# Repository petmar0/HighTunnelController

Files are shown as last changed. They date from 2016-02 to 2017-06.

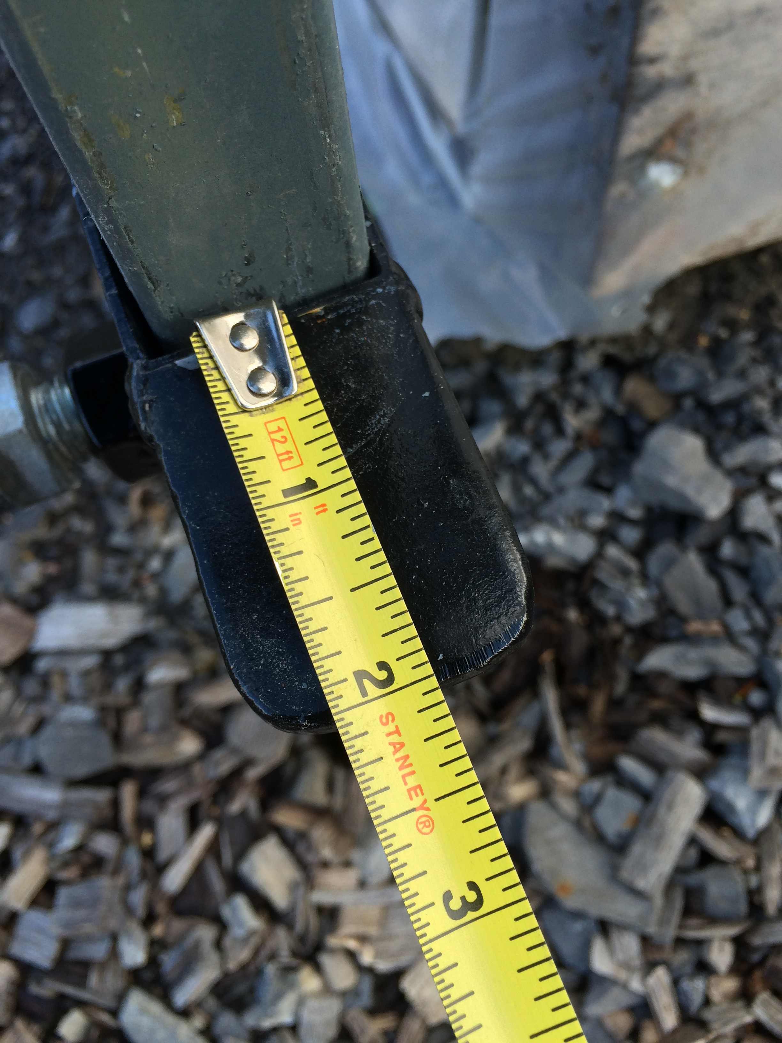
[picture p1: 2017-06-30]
TheManInTheHighTunnel/Winch Measurements 2.JPG

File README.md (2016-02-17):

# HighTunnelController

Control Flow
The setup method configures SD card and reads config file values from live.cfg
If you want to change config values you can edit live.cfg on the SD card manually or use the program to edit it

After starting up the program outputs instructions to the serial monitor and waits for your input 
* You can (and should) set the date/time
* You can read sensor values to test the sensors out
* You can control the motors to test them out
* You can read and erase the config file and the log file
* You can write new values to the config file
* You can start the main high tunnel control program running

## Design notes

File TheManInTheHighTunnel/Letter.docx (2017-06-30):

Pete Marchetto

160B Riley Robb Hall

111 Wing Dr.

Ithaca, NY 14853

201.403.5470

pmm223@cornell.edu

October 29, 2015

Dr. Joshua Cerra

444 Kennedy Hall

Ithaca, NY 14853

Dear Dr. Cerra,

This letter is to confirm the specification that we discussed yesterday. You are asking for a system that is capable of controlling the temperature within a high tunnel to stay a set amount above the external ambient temperature.

The system:

- shall be capable of regulating the internal temperature of a high tunnel to stay at 5.0±0.5 °F above the external ambient temperature.
- shall be capable of operating in temperatures between -20 to 130 °F.
- shall make use of two winches (T2000, SuperWinch, Putnam, CT), each of which consumes a maximum of 0.5 kW, to trim the wall height of the high tunnel for ventilation and heating or cooling.
- shall further use two ventilation fans (yet to be specified) to draw in air at a rate no less than 500 CFM to cool the high tunnel.
- shall be capable of running on solar power only in an environment with a maximum insolation power of 2 kWh/m²/Day (NREL, 2005).
- shall be fully compliant with the IP66W rating, and shall have its sensitive electronics enclosed in a NEMA 4 or 4X series enclosure.
- shall have a thermal mass element to keep temperatures sufficiently high at night comprised of a minimum of 3 gal./sqft. for the south wall of the high tunnel, comprising a total of 15 55 gallon drums or 20 35 gallon drums.

Please review this specification and get back to me with any comments or corrections so that we might proceed expeditiously to component selection.

Sincerely,

Pete Marchetto

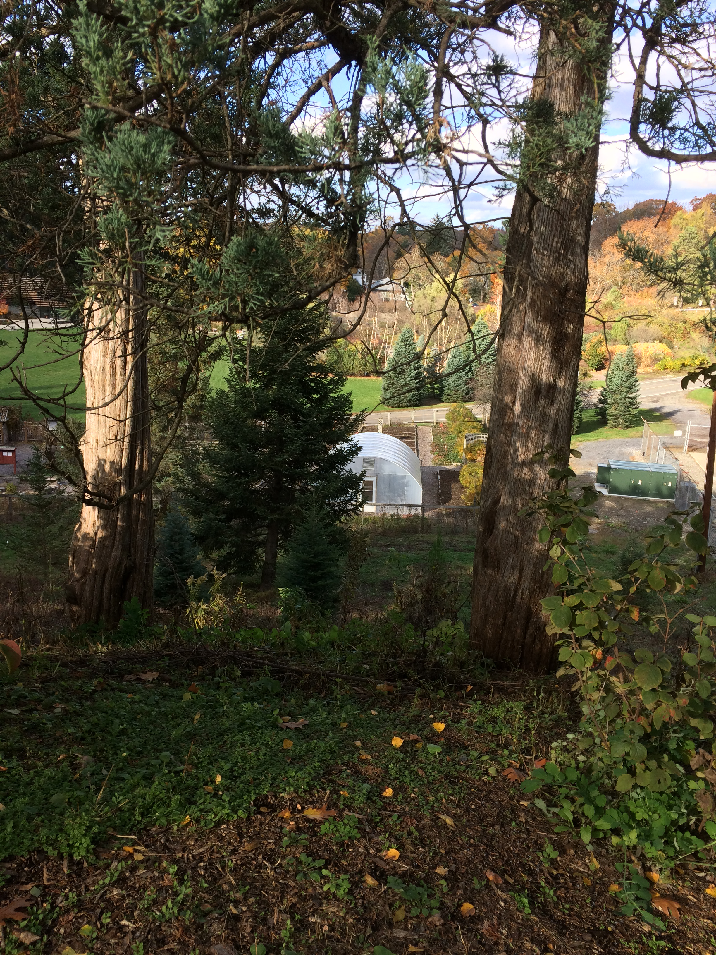
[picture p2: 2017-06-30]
TheManInTheHighTunnel/Sunlight from Above 2.JPG

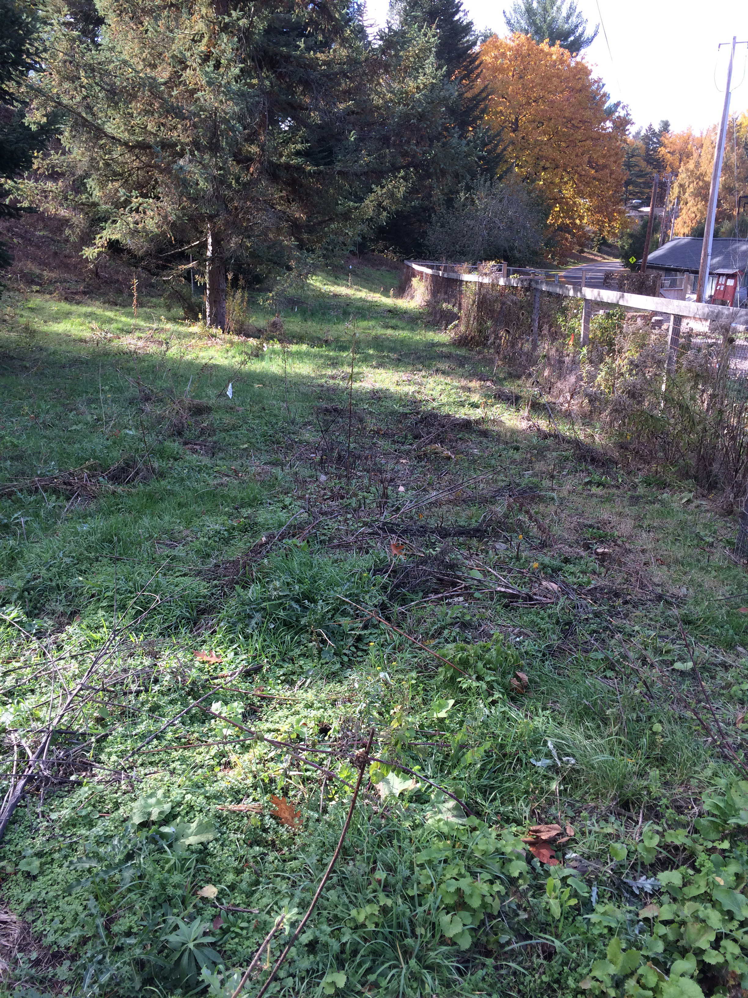
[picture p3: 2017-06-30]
TheManInTheHighTunnel/Sunlight on Fence 5.JPG

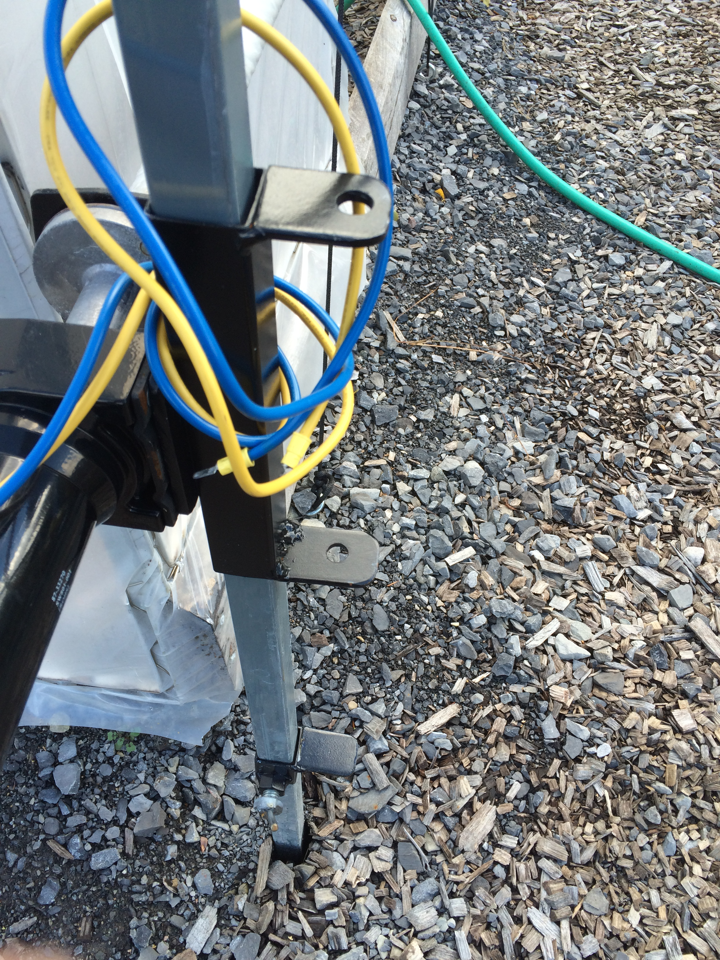
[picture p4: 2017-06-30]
TheManInTheHighTunnel/Winch Detail 1.JPG

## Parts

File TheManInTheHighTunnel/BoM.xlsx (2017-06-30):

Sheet: Summary
Sensing | $800.00
Enclosure | $300.00
Power | $1865.00
Control | $320.00
Fans | $940.00
Thermal | $130.00
Total | $4355.00

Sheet: Enclosure
Item | Make | Model | Quantity | Price |  | Extended Price | URL | Dimensions | Purpose
Waterproof Box | Pelican | iM2100 | 2 | $100.00 | not ordered | $200.00 | http://www.pelican.com/us/en/product/watertight-storm-hard-cases/small-case/standard/iM2100/ | At least 10x14x6 | Keep circuits safe and dry | Did not order - need to find dealer in this area
High Current (45A 12V min) 2 wire connectors | Conxall/Switchcraft | 4182-2PG-300 | 10 | $10.00 | not ordered | $100.00 | http://www.digikey.com/product-search/en?keywords=4182-2PG-300 |  | Connectors for motors and actuators | Not clear what needs to be ordered
Low Current (1A) 2 wire connectors | Amico | M14-4 | 10 | $15.00 | not ordered | $150.00 | http://www.amazon.com/M14-4-Waterproof-Connector-Connect-Adpater/dp/B00HR6M98Q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 |  | Connectors for limit switches and PV monitor | Not clear what needs to be ordered
Low Current (1A) 3 wire connectors | Amico | M14-4 | 10 | $15.00 | not ordered | $150.00 | http://www.amazon.com/M14-4-Waterproof-Connector-Connect-Adpater/dp/B00HR6M98Q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 |  | Connectors for temperature sensors
Super High Current (85 A 12V min) 2 wire connector | Conxall/Switchcraft | 4182-2PG-300 | 2 | $10.00 | not ordered | $20.00 | http://www.digikey.com/product-search/en?keywords=4182-2PG-300 |  | Connector for battery
Total |  |  |  |  |  | $300.00

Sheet: Power
Item | Make | Model | Quantity | Price |  | Extended Price | URL | Notes
backup battery | ExpertPower | EXPT1250 | 1 | $20.00 | ordered | $20.00 | http://www.amazon.com/ExpertPower-EXP1270-Black-Rechargeable-Battery/dp/B003S1RQ2S | sealed lead acid battery (12V, 6Amh)
Marine Deep Cycle Battery | VMAXTANKS | MR-86-50 | 2 | $150.00 | ordered | $300.00 | http://www.amazon.com/VMAXTANKS-MR86-50-Performance-Navigator-Trolling/dp/B009UE6NY4 | 50 Amh, 12 V
thin wire |  |  | 1 | $30.00 | not ordered | $30.00 | http://www.grainger.com/product/GRAINGER-APPROVED-Music-Wire-5XE99?s_pp=false | 16 gage or lower, 2 conductor, 250 feet
heavy duty wire |  |  | 1 | $300.00 | not ordered | $300.00 | http://www.grainger.com/product/AFC-MC-CABLES-12-AWG-Armored-Cables-WP5969589/_/N-/Ntt-armored+cables+12-2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 | armored cable, 16 gage or lower, 2 conductor, 250 feet
heavy duty hi amp wire |  |  | 1 | $150.00 | not ordered | $150.00 | http://www.grainger.com/category/building-wire/wire-and-cable/wire-cable-and-carrier-systems/electrical/ecatalog/N-qs4Z1z0mlns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 | 6WG or lower, exterior, 1 conductor, 150 feet
charge controller | Renogy |  | 1 | $45.00 | ordered | $45.00 | http://www.amazon.com/Renogy-Amp-Solar-Charge-Controller/dp/B00BCTLIHC | 20 amh
Panels | Renogy |  | 6 | $150.00 | only ordered 2 | $900.00 | http://www.amazon.com/Renogy-Watts-Volts-Monocrystalline-Solar/dp/B009Z6CW7O | 100 W
Cable Connectors (45 A) | Connxall | 3182-2SG-3DC | 10 | $10.00 | not ordered | $100.00 | http://www.mouser.com/Search/Refine.aspx?Keyword=3182-2SG-3DC
Cable Connectors (85 A) | Connxall | 3282-4SG-3DC | 2 | $10.00 | not ordered | $20.00 | http://www.mouser.com/ProductDetail/Conxall-Switchcraft/6282-4SG-3DC/?qs=I3kMT7EEIOUfaAjga64oJA%3D%3D
Total |  |  |  |  |  | $1865.00

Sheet: Sensing
Item | Make | Model | Quantity | Price |  | Extended Price | URL
Temp Sensor | Texas Instruments | LM35CAZ/NOPB-ND | 10 | $10.00 | not ordered | $100.00 | http://www.digikey.com/product-detail/en/LM35CAZ%2FNOPB/LM35CAZ%2FNOPB-ND/148180
Limit Switch | Panasonic | AZH2332 | 10 | $40.00 | not ordered | $400.00 | http://www.digikey.com/product-search/en?keywords=azh2332
Cable Connector Cord | Panasonic | AZH28113 | 10 | $30.00 | not ordered | $300.00 | http://www.digikey.com/product-search/en?keywords=AZH28113
Total |  |  |  |  |  | $800.00

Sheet: Control
Item | Make | Model | Quantity | Price |  | Extended Price | URL | Dimensions
Relay | Sainsmart | B0057OC66U | 10 | $20.00 | ordered 5 | $200.00 | http://www.amazon.com/gp/product/B0057OC66U/ | 8x6x2
Board | Wildfire | v3 | 2 | $50.00 | ordered | $100.00 | http://shop.wickeddevice.com/product/wildfire/ | 4x3x2
PIR Sensors | MPJA | HC-SR501 | 10 | $2.00 | ordered 4 | $20.00 | http://www.amazon.com/2013newestseller-HC-SR501-Pyroelectric-Infrared-Detector/dp/B00FDPO9B8?rps=1
Total |  |  |  |  |  | $320.00

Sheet: Fans
Item | Make | Model | Quantity | Price |  | Extended Price | URL
Actuators | CfD | CFD-DLA2 | 2 | $10.00 | ordered | $20.00 | http://www.amazon.com/gp/product/B00CZBQCR2
Fans | Backwoods Solar | F20-PLUS | 2 | $460.00 | ordered | $920.00 | http://www.backwoodssolar.com/products/fans-large-small/large-dc-super-fan-20inch-12-24v
Total |  |  |  |  |  | $940.00

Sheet: Thermal
Item | Make | Model | Quantity | Price |  | Extended Price | URL
Lime | Espoma | GL6 | 2 | $5 | ordered | $10 | http://www.amazon.com/Espoma-GL6-Garden-Amendment-6-75-Pound/dp/B0063ZDTI6
Barrels |  | 35 Gal. | 2 | $40 |  | $80
Hose | Gilmour | Flexogen 100 | 1 | $40 | ordered | $40 | http://www.amazon.com/Gilmour-Flexogen-Hose-Inch-10012100/dp/B000NCWOKE
Total |  |  |  |  |  | $130

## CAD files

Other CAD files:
TheManInTheHighTunnel/Thermal Mass System.skp

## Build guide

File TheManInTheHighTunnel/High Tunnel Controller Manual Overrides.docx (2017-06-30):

High Tunnel Controller Manual Overrides

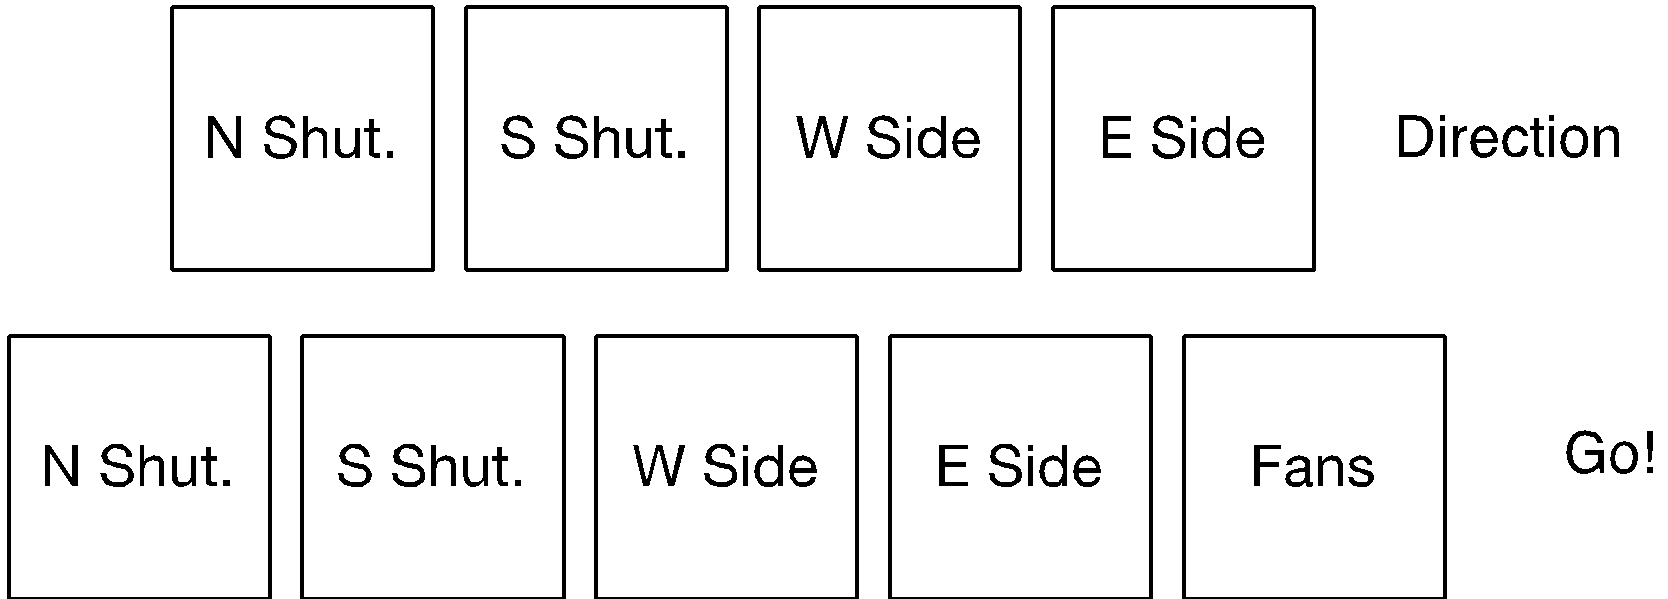
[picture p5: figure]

Default direction states: shutters, opening; sides, closing.

To open shutters, press their go relays (bottom row). To close shutters, hold down their direction relays (top row) while pressing their go relays. The return springs should hold the shutters in their last set position.

To close sides, press their go relays (bottom row). To open sides, hold down their direction relays (top row) while pressing their go relays.

The fans can only be turned on momentarily by manually overriding their go relay, but this is useful for testing them.

WARNING: There are no limit controls or safety devices to stop the sides when they are engaged manually. Make certain that all people in the vicinity are clear, and that you stop the sides before they reach their upward or downward limit of travel.

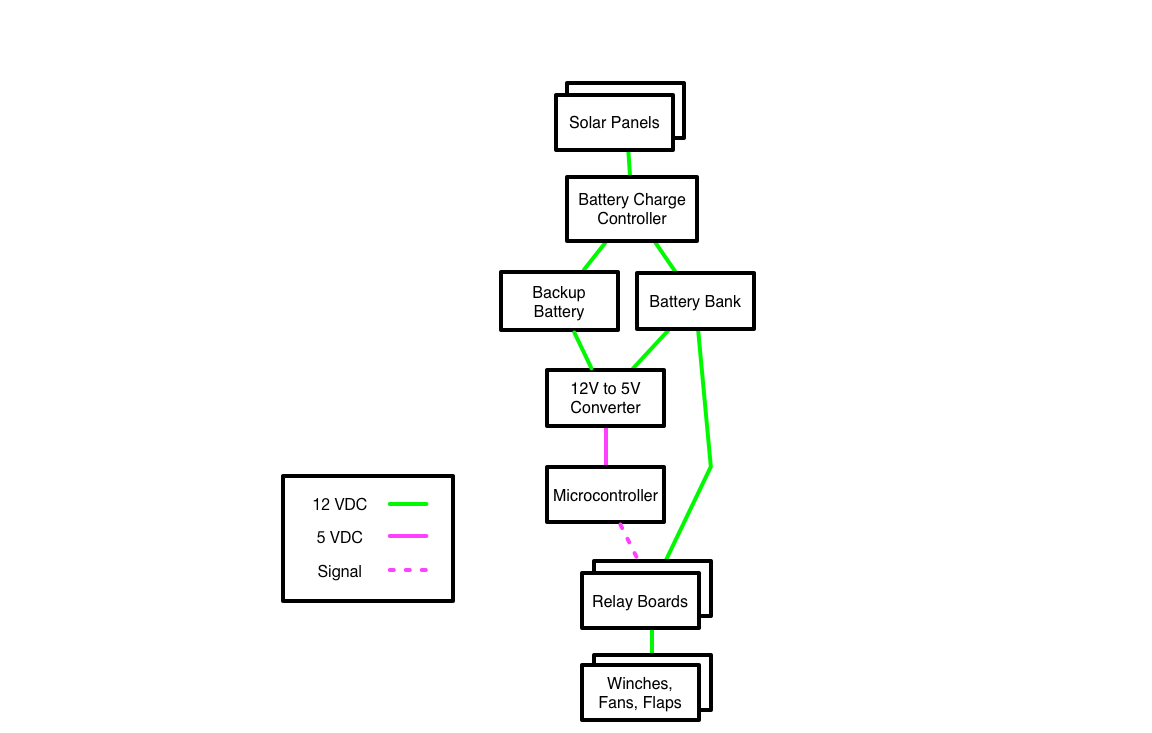
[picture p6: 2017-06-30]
TheManInTheHighTunnel/Power/power wiring diagram.png

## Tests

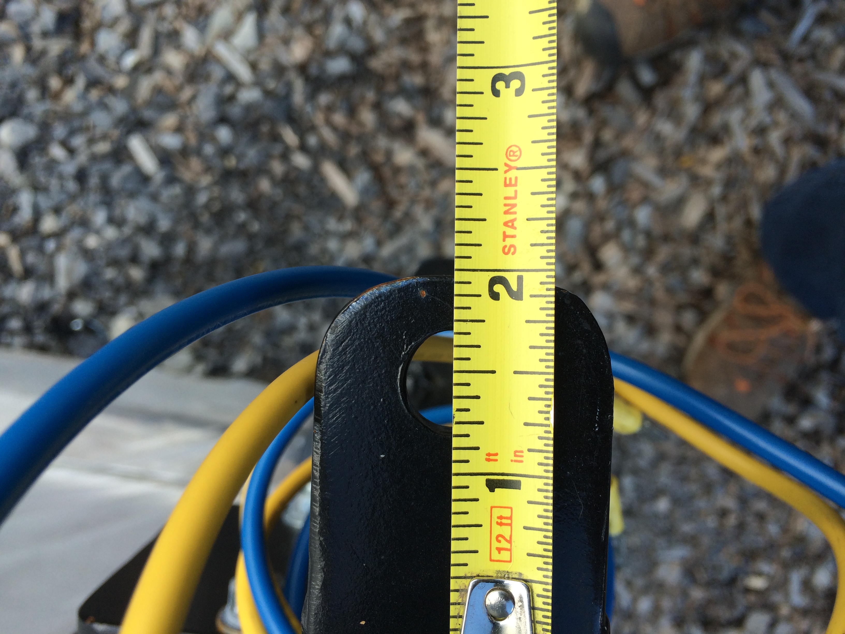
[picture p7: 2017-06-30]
TheManInTheHighTunnel/Winch Measurements 3.JPG

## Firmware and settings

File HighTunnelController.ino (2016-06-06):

#include <Time.h>
#include <SD.h>
#include <WildFire.h>
#include <Wire.h>
// #include "RTClib.h"

// Constants used by program, note that the file names are essentially constants but specifying that causes an error
const unsigned long MIN_ALLOWABLE_DATE_TIME = 1420156799; // 1 second before Jan 1 2015 GMT
const unsigned long MAX_ALLOWABLE_DATE_TIME = 1893520800; // Jan 1 2030 GMT
const unsigned long SECONDS_IN_HOUR         = 3600;
char configFileName[] = "live.cfg"; // recommended to leave this set and rename a different file as live.cfg to update it
char logFileName[] = "live.log"; // recommended to leave this set.  Multiple log files will be spun off as we go.
char heatWaveFileName[] = "heat.log"; // recommended to leave this set. This is where heatwave data is logged explicitly.

// External variables that can be passed in via config file
int gmt_hour_offset = -5; // -5 is the EST offset
float too_hot_delta = 6.0;  // If difference between inside and outside temp is more than this start to cool
float way_too_hot_delta = 7.5; // If difference between inside and outside temp is more than this use more aggressive cooling measures
float too_cool_delta = 4.0; // If difference between inside and outside temp is less than this start to warm
float super_cool_delta = -1.0; // If difference between inside and outside temp is less than this and warm up inside using outside air
boolean disable_log_file = false; // setting this to true disables writing to log file. Can help debug memory card issues
boolean manual_sensor_entry_mode = false; // If true then read sensors from Serial input by user instead of actual sensors.  Used to test system.
char temperature_units = 'F'; // Set ot F for Farenheight of C for Celcius.  If you change this you should probably change the deltas too.
int heat_wave_temperature = 90; // Temperature at which tunnel is considered a heatwave. WARNING if you update temperature units to C you MUST update this as well
int heat_wave_enabled_warming_temperature = 95; // When heat wave is enabled keep warming tunnel till it hits this. Should be enough above heat_wave_temperature to ensure it doesm't cool down below it
int heat_wave_enabled_cooling_temperature = 99; // When heat wave is enabled cool if tunnel gets above this. If outside is hot the keep up with that temp instead
int heat_wave_hours_to_log = 6; // How many consecutive hours temp must be above heat_wave_temperature to count as a heat wave day
int heat_wave_days_to_log = 3; // How many consecutive heat wave days must happen to count as a heat wave
int heat_wave_switch_pin = 12; // Pin the switch to enable heat wave mode is connected to
int pir_sensor_pin = A6; // Pin that PIR motion sensors that ensure no one is around while sides roll are connected to.
int pir_wait_time_max_seconds = 10; //If PIR sensors detect someone this is how long we'll wait before we give up and accept that we cannot roll
int pir_milliseconds_between_checks = 1000; //How long to wait between sampling the PIR sensors again when someone is detected, also how long to do a continuous sample for movement
int inside_temp_sensor_pin = A2; // Analog pin that temperature sensor inside the high tunnel is connected to
int outside_temp_sensor_pin = A1; // Analog pin that temperature sensor outside the high tunnel is connected to
unsigned long millisecond_delay_between_actions = 5000; // How long to wait between reading temperature and taking action to correct it
int winch_roll_seconds = 7; // How many seconds to roll each winch at a time
int winch_roll_milliseconds_between_limit_check = 100; // How long to wait between checking limit sensors while rolling
int fan_run_seconds = 20; // How how long to run fans at a stretch
int east_winch_roll_direction_digital_pin = 3; // Digital pin that sets direction east winch will roll, also sounds alarm when powered up
int east_winch_roll_power_digital_pin = 4; // Digital pin that causes east winch to start rolling
int west_winch_roll_direction_digital_pin = 11; // Digital pin that sets direction west winch will roll, also sounds alarm when powered up
int west_winch_roll_power_digital_pin = 5; // Digital pin that causes west winch to start rolling
int east_winch_limit_pin = A3; // Analog pin that connects to top limit sensor for east winch
int west_winch_limit_pin = A0; // Analog pin that connects to top limit sensor for west winch
int south_shutters_direction_digital_pin = 7; // Digital pin that controls whether south shutters open or close
int south_shutters_power_digital_pin = 8; // Digital pin that powers south shutters to move open or closed
int north_shutters_direction_digital_pin = 9; // Digital pin that controls whether north shutters open or close
int north_shutters_power_digital_pin = 10; // Digital pin that powers north shutters to move open or closed
int fan_power_digital_pin = 2; // Digital pin that powers up the fans to spin
int solar_sensor_pin = A7; // Analog pin that senses how much power the solar panel is delivering
boolean automatically_start_high_tunnel_control = false; // Set this to true so that upon restart the high tunnel control program automatically runs

// Internal variables that the program manages itself
boolean sdCardWorking = false;
boolean runFansNext = true; // Used to alternate between running fans and rolling sides
boolean shuttersOpen = false; // Used to track shutter status
int heatWaveRequiredEndTime = 0; // Store the hour/minute when you'll know a heatwave has lasted long enough to be counted for the day
boolean heatWaveTempSurpassedToday = false; // If we ever go above heat wave temp for a moment today note it
boolean heatWaveHoursSurpassedToday = false; // If it has stayed above heat_wave_temperature for heat_wave_hours_to_log then note it
int heatWaveDaysInARow = 0; // Count how many days we have had heatWaveHoursSurpassedToday in a row
int heatWaveVarsResetDay = 0; // Note the last day that heatwave vars were reset, if it isn't today log heatwave data and reset vars
boolean sd_write_enabled = false; // Debugging variable that can be used to temporarily disable writing to SD card
boolean sd_read_enabled = false; // Debugging variable that can be used to temporarily disable writing to SD card
WildFire wf;
// RTC_DS1307 rtc;

////////////////////////Start SD Card Functions////////////////////////
void setupSdCard() {
  Serial.print(F("SD Card Initializating..."));        
  if (!SD.begin(16)) {
    Serial.println(F("SD Init Failed!"));
    sdCardWorking = false;
  }
  else{
    Serial.println(F("SD Init Complete."));
    sdCardWorking = true;
  }
}

void ensureLogFileExists (char sdFileName[]) {
  if (sd_read_enabled) {
    Serial.println("Ensuring file exists on SD Card.  Filename=" + String(sdFileName));
    File myFile = SD.open(sdFileName, FILE_READ);
    if (myFile) {
      myFile.close();
      logMessage("File found: " + String(sdFileName));
    }
    else {
      logMessage("File not found: " + String(sdFileName));
      writeSdFile("Initializing File: " + String(sdFileName), sdFileName);
    }
    myFile = SD.open(sdFileName, FILE_READ);
    if (!myFile)
      logError("Problem creating file: " + String(sdFileName));
    myFile.close();
  }
  else
    Serial.println("SD Reading disabled, no log file exists");
}

void readConfigFromFile () {
  if (sd_read_enabled) {
    File configFile;
    configFile = SD.open(configFileName, FILE_READ);
    if (configFile) {
      logMessage("Reading config file " + String(configFileName));
        
      // read key value pairs from the file until there's nothing else in it:
      while (configFile.available()) {
        String key = configFile.readStringUntil('=');
        String value = configFile.readStringUntil('\n');
        processKeyValuePair(key,value,false);
      }
      // close the file:
      configFile.close();
    } else 
      logMessage("Error opening config file " + String(configFileName));
  }
  else
    Serial.println("SD Reading disabled, so no reading config file.");
}

int processConfigInt (String key, String value) {
  float output = value.toInt();
  logMessage("Config File setting " + key + " to int " + String(output));
  return output;
}

float processConfigFloat (String key, String value) {
  float output = value.toFloat();
  logMessage("Config File setting " + key + " to float " + String(output));
  return output;
}

boolean processConfigBool (String key, String value) {
  boolean output = confirmValidBool(value, true, false);
  logMessage ("Config File setting " + key + " to boolean " + String(output)); 
  return output;
}

boolean validKey (String key, String desiredKey, boolean printOutMode) {
  if (printOutMode) {
    Serial.print (desiredKey + " is a valid key");
    return true;
  }
  if (key == desiredKey)
    return true;
  return false;
}

// printOutMode is used to print a list of keys and what qualifies as valid for each to the terminal for reference.
// coding it this way means that the list of keys and validity is printed directly from this procedure so as new
// keys are added or validity conditions are updated it will always print out correct output.
void processKeyValuePair(String key, String value, boolean printOutMode) {
  if (!printOutMode)
    logMessage("Processing key value pair of key=" + key + " value=" + value);
  if (validKey(key, "gmt_hour_offset", printOutMode) && confirmValidNum(value,true,false, printOutMode))
    gmt_hour_offset = processConfigInt(key,value);
  else if (validKey(key, "too_hot_delta", printOutMode) && confirmValidNum(value,false,true, printOutMode))
    too_hot_delta = processConfigFloat(key,value);
  else if (validKey(key, "way_too_hot_delta", printOutMode) && confirmValidNum(value,false,true, printOutMode))
    way_too_hot_delta = processConfigFloat(key,value);
  else if (validKey(key, "too_cool_delta", printOutMode) && confirmValidNum(value,false,true, printOutMode))
    too_cool_delta = processConfigFloat(key,value);
  else if (validKey(key, "super_cool_delta", printOutMode) && confirmValidNum(value,true,true, printOutMode))
    super_cool_delta = processConfigFloat(key,value);
  else if (validKey(key, "inside_temp_sensor_pin", printOutMode) && confirmValidNum(value,false,false, printOutMode))
    inside_temp_sensor_pin = processConfigInt(key,value);
  else if (validKey(key, "outside_temp_sensor_pin", printOutMode) && confirmValidNum(value,false,false, printOutMode))
    outside_temp_sensor_pin = processConfigInt(key,value);
  else if (validKey(key, "disable_log_file", printOutMode) && confirmValidBool(value, false, printOutMode))
    disable_log_file = processConfigBool(key,value);
  else if (validKey(key, "manual_sensor_entry_mode", printOutMode) && confirmValidBool(value, false, printOutMode))
    manual_sensor_entry_mode = processConfigBool(key,value);
  else if (validKey(key, "temperature_units", printOutMode) && confirmValidTemperatureUnit(value, printOutMode))
    temperature_units = value.charAt(0);
  else if (validKey(key, "heat_wave_temperature", printOutMode) && confirmValidNum(value,false,false, printOutMode))
    heat_wave_temperature = processConfigInt(key,value);
  else if (validKey(key, "heat_wave_enabled_warming_temperature", printOutMode) && confirmValidNum(value,false,false, printOutMode))
    heat_wave_enabled_warming_temperature = processConfigInt(key,value);
  else if (validKey(key, "heat_wave_enabled_cooling_temperature", printOutMode) && confirmValidNum(value,false,false, printOutMode))
    heat_wave_enabled_cooling_temperature = processConfigInt(key,value);
  else if (validKey(key, "heat_wave_hours_to_log", printOutMode) && confirmValidNum(value,false,false, printOutMode))
    heat_wave_hours_to_log = processConfigInt(key,value);
  else if (validKey(key, "heat_wave_days_to_log", printOutMode) && confirmValidNum(value,false,false, printOutMode))
    heat_wave_days_to_log = processConfigInt(key,value);
  else if (validKey(key, "heat_wave_switch_pin", printOutMode) && confirmValidNum(value,false,false, printOutMode))
    heat_wave_switch_pin = processConfigInt(key,value);
  else if (validKey(key, "pir_sensor_pin", printOutMode) && confirmValidNum(value,false,false, printOutMode))
    pir_sensor_pin = processConfigInt(key,value);
  else if (validKey(key, "pir_wait_time_max_seconds", printOutMode) && confirmValidNum(value,false,false, printOutMode))
    pir_wait_time_max_seconds = processConfigInt(key,value);
  else if (validKey(key, "pir_milliseconds_between_checks", printOutMode) && confirmValidNum(value,false,false, printOutMode))
    pir_milliseconds_between_checks = processConfigInt(key,value);    
  else if (validKey(key, "millisecond_delay_between_actions", printOutMode) && confirmValidNum(value,false,false,printOutMode))
    millisecond_delay_between_actions = processConfigInt(key,value);
  else if (validKey(key, "winch_roll_seconds", printOutMode) && confirmValidNum(value,false,false,printOutMode))
    winch_roll_seconds = processConfigInt(key,value);
  else if (validKey(key, "winch_roll_milliseconds_between_limit_check", printOutMode) && confirmValidNum(value,false,false,printOutMode))
    winch_roll_milliseconds_between_limit_check = processConfigInt(key,value);
  else if (validKey(key, "fan_run_seconds", printOutMode) && confirmValidNum(value,false,false,printOutMode))
    fan_run_seconds = processConfigInt(key,value);
  else if (validKey(key, "east_winch_roll_direction_digital_pin", printOutMode) && confirmValidNum(value,false,false,printOutMode))
    east_winch_roll_direction_digital_pin = processConfigInt(key,value);
  else if (validKey(key, "east_winch_roll_power_digital_pin", printOutMode) && confirmValidNum(value,false,false,printOutMode))
    east_winch_roll_power_digital_pin = processConfigInt(key,value);
  else if (validKey(key, "west_winch_roll_direction_digital_pin", printOutMode) && confirmValidNum(value,false,false,printOutMode))
    west_winch_roll_direction_digital_pin = processConfigInt(key,value);
  else if (validKey(key, "west_winch_roll_power_digital_pin", printOutMode) && confirmValidNum(value,false,false,printOutMode))
    west_winch_roll_power_digital_pin = processConfigInt(key,value);
  else if (validKey(key, "east_winch_limit_pin", printOutMode) && confirmValidNum(value,false,false,printOutMode))
    east_winch_limit_pin = processConfigInt(key,value);
  else if (validKey(key, "west_winch_limit_pin", printOutMode) && confirmValidNum(value,false,false,printOutMode))
    west_winch_limit_pin = processConfigInt(key,value);
  else if (validKey(key, "south_shutters_direction_digital_pin", printOutMode) && confirmValidNum(value,false,false,printOutMode))
    south_shutters_direction_digital_pin = processConfigInt(key,value);
  else if (validKey(key, "south_shutters_power_digital_pin", printOutMode) && confirmValidNum(value,false,false,printOutMode))
    south_shutters_power_digital_pin = processConfigInt(key,value);
  else if (validKey(key, "north_shutters_direction_digital_pin", printOutMode) && confirmValidNum(value,false,false,printOutMode))
    north_shutters_direction_digital_pin = processConfigInt(key,value);
  else if (validKey(key, "north_shutters_power_digital_pin", printOutMode) && confirmValidNum(value,false,false,printOutMode))
    north_shutters_power_digital_pin = processConfigInt(key,value);
  else if (validKey(key, "fan_power_digital_pin", printOutMode) && confirmValidNum(value,false,false,printOutMode))
    fan_power_digital_pin = processConfigInt(key,value);
  else if (validKey(key, "solar_sensor_pin", printOutMode) && confirmValidNum(value,false,false,printOutMode))
    solar_sensor_pin = processConfigInt(key,value);
  else if (validKey(key, "automatically_start_high_tunnel_control", printOutMode) && confirmValidBool(value, false, printOutMode))
    automatically_start_high_tunnel_control = processConfigBool(key,value);
  else if (!printOutMode)
    logMessage("key:'" + key + "' is not valid.  Ignoring value:'" + value + "'");
}

boolean confirmValidTemperatureUnit(String str, boolean printOutMode) {
  if (printOutMode)
    Serial.println (" its value must be F or C");
  if (str.charAt(0) == 'F' or str.charAt(0) == 'C')
    return true;
  return false;
}

// returnParsedValue lets this function return the actual parsed boolean value of the string
// this allows us to avoid duplicating the boolean string processing code in processConfigBool which could lead to errors
boolean confirmValidBool(String str, boolean returnParsedValue, boolean printOutMode) {
  if (printOutMode)
    Serial.println (" its value must be a boolean (true, false, t, f, 1, or 0)");
  if (str.equalsIgnoreCase("true") or str.equalsIgnoreCase("t") or str.equalsIgnoreCase("1"))
    return true;
  if (str.equalsIgnoreCase("false") or str.equalsIgnoreCase("f") or str.equalsIgnoreCase("0")) {
    if (returnParsedValue)
      return false;
    else
      return true;
  }
  return false;
}

boolean confirmValidNum(String str, boolean allowNegative, boolean allowDecimalPoint, boolean printOutMode) {
  if (printOutMode) {
    if (allowDecimalPoint)
      Serial.print (" its value must be a decimal number (exe. 2.34)");
    else
      Serial.print (" its value must be an integer number (exe. 2)");
    if (!allowNegative)
      Serial.print (" at or above zero");
    Serial.println();
  }
  boolean isValidNum=false;
  boolean oneDecimalFound=false;
  int i = 0;
  // if we want to allow negatives and the first char is a minus sign ignore it, if we do not want to allow negatives log specific error
  if (str.charAt(0) == '-') 
    if (allowNegative)
      i=1;
    else {
      logError("Negative values not allowed!  Value " + str + " is invalid");
      return false;
    }
  for(i;i<str.length();i++)
  {
    isValidNum = isDigit(str.charAt(i));
    if(!isValidNum)
    {
      // optionally allow on decimal point in string, but it cannot be the only character in the string
      if (allowDecimalPoint && str.length()!=1 && str.charAt(i) == '.') {
        if (oneDecimalFound) {
          logError("Second . found in string " + str + " that we're trying to convert to numeric");
          return false;
        }
        oneDecimalFound = true;
        isValidNum = true;
      }
      else {
        logError("Non digit " + String(str.charAt(i)) + " at position " + String(i) + " in string that should be numeric");
        return false;
      }
    }
  }
  return isValidNum;
}

void writeSdFile(String sdMessage, char sdFileName[]) {
  File myFile;
  Serial.print("Writing to file " + String(sdFileName));
  Serial.println(" Message: " + sdMessage);
  if (sd_write_enabled) {
    myFile = SD.open(sdFileName, FILE_WRITE);
    if (myFile) {
      myFile.println(sdMessage);
      myFile.close();
    }
    else 
      Serial.println("WRITE ERROR: Issue opening file for writing!");
  }
}

void readSdFile(char sdFileName[])
{
  if (sd_read_enabled) {
    File myFile;
    logMessage("Reading file to Serial: " + String(sdFileName));
    myFile = SD.open(sdFileName, FILE_READ);
    if (myFile) {
      while (myFile.available()) {
        Serial.write(myFile.read());
      }
      myFile.close();
    }
    else
      logError("Issue opening file for reading!");
  }
  else
    Serial.println("SD Reading disabled, so no reading file.");

}

void emptySdFile(char sdFileName[], String confirmationString){
  File myFile;
  if (confirmationString.equals("Y")) {
    logMessage("Emptying data from file " + String(sdFileName));
    SD.remove(sdFileName);
    // After file has been deleted recreate an empty version of it.
    myFile = SD.open(sdFileName, FILE_WRITE);
    myFile.close();
  }
  else
    Serial.println("You tried to enter a command to empty a file but did not include the required Y after the command name");
}

void printFilesInBaseSdDirectory() {
  logMessage("Printing files in base SD directory to Serial");
  File dir = SD.open("/");
  while (true) {
    File entry =  dir.openNextFile();
    if (! entry) {
      // no more files
      break;
    }
    Serial.print(entry.name());
    if (!entry.isDirectory()) {
      Serial.print("\t");
      Serial.println(entry.size(), DEC);
    }
    entry.close();
  }
  dir.close();
}
////////////////////////End SD Card Functions////////////////////////

////////////////////////Start Log and Serial Interface Functions////////////////////////
// method for logging errors.  Ensures they are all prefaced with the same text and can be modified for easier debugging
void logError(String message) {
  logMessage("ERROR: " + message);
}

void logMessage(String message) {
  if (disable_log_file)
    Serial.println(getTimeStampString() + "- UNLOGGED -" + message);
  else
    writeSdFile(getTimeStampString() + "-" + message, logFileName);
}

void logHeatWave(String message) {
  writeSdFile(getTimeStampString() + "-" + message, heatWaveFileName);
}
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
void loop() {
  char incomingByte;
  setDigitalPinModes(false);
  if (automatically_start_high_tunnel_control)
    processSerialInput('b');
    
  if (Serial.available() > 0){
    delay(100);
    incomingByte = Serial.read();
    Serial.print("     Command received: ");
    Serial.println(incomingByte);
    processSerialInput(incomingByte);
  }
}

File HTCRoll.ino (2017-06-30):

#include "math.h"                           //Get the math library for math functions
#include "SparkFunPhant/SparkFunPhant.h"    //Get the Phant library for Phant functions

const char server[] = "data.sparkfun.com"; // Phant destination server
const char publicKey[] = "YGoKdGpEZ2TOJ4Wzw5nW"; // Phant public key
const char privateKey[] = "RbdJBbEVNlCXEpbqN64b"; // Phant private key
Phant phant(server, publicKey, privateKey); // Create a Phant object
unsigned long lastPost = 0; // global variable to keep track of last post time

int FanPin=2;    //Pin that the fan relays are wired to
int EDirPin=3;    //Pin that the east winch directional relays are wired to
int EGoPin=4;   //Pin that the east winch go relays are wired to
int WDirPin=5;    //Pin that the west winch directional relays are wired to
int WGoPin=6;   //Pin that the west winch go relays are wired to
int ToutPin=A0;   //Pin that the outside thermistor is wired to
int TinPin=A1;    //Pin that the inside thermistor is wired to
int LimPin=A2;    //Pin that the winch limit switches are wired to
int PIRPin=A4;    //Pin that the PIR motion sensors are wired to
int SolarPin=A5;  //Pin that the solar panel voltage divider is wired to
int TboxPin=A6;   //Pin that the control box thermistor is wired to
int HWSwitch=7;   //Pin that the heat wave switch is wired to

int dly=10;     //Hysteresis delay for all functions (sec)
float thresh=5.5; //Temperature delta threshold setpoint float (°F)
float HWThresh=96;  //Heat wave threshold setpoint float (°F)
float k1=0.054; //Slope constant for thermistors (°F/LSB)
float k2=10;          //Offset constant for thermistors (°F)
int POST_RATE=1000*dly; //The post rate in msec is equal to 1000 times the dly in seconds
int SideTime=100;    //Timer variable for when the sides should roll up

boolean HW=FALSE; //Heat wave storage boolean
int PIR=0;      //PIR value storage int
int Lim=0;      //East limit switch storage int
int SideTimer=0;    //Storage variable for side timer
int WSideState=0;   //State of the west side roll
int ESideState=0;   //State of the east side roll
float Tout=0;   //Outside temperature storage float
float Tin=0;    //Inside temperature storage float
float Tbox=0;   //Control box temperature storage float
float deltaT=0;   //Temperature difference storage float
float Solar=0;    //Solar panel output storage float

void setup(){
  Particle.publish("ROBOT ENERGIZED");    //Update status on Particle dashboard
  Time.zone(-4);                            //Set the time zone as EDT
  pinMode(FanPin, OUTPUT);                //Set the fan pin as an output
  pinMode(EDirPin, OUTPUT);               //Set the east winch direction pin as an output
  pinMode(EGoPin, OUTPUT);                //Set the east winch go pin as an output
  pinMode(WDirPin, OUTPUT);               //Set the west winch direction pin as an output
  pinMode(WGoPin, OUTPUT);                //Set the west winch go pin as an output
  pinMode(ToutPin, INPUT);                //Set the outside thermistor pin as an input
  pinMode(TinPin, INPUT);                 //Set the inside thermistor pin as an input
  pinMode(LimPin, INPUT);                //Set the east limit switch pin as an input
  pinMode(PIRPin, INPUT);                 //Set the PIR sensor pin as an input
  pinMode(SolarPin, INPUT);               //Set the solar panel voltage divider pin as an input
  pinMode(TboxPin, INPUT);                //Set the control box thermistor pin as an input
  pinMode(HWSwitch, INPUT);               //Set the heat wave switch pin as an input
  digitalWrite(FanPin, HIGH);             //Put the fan relays to off state
  digitalWrite(EDirPin, HIGH);            //Put the east directional relays to off state
  digitalWrite(EGoPin, HIGH);             //Put the east go relays to off state
  digitalWrite(WDirPin, HIGH);            //Put the west directional relays to off state
  digitalWrite(WGoPin, HIGH);             //Put the west go relays to off state
}
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

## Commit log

2016-01-23 Adding stubs for running fans and opening shutters, removing unneeded Wire.h and updating time so it stores time in GMT and only adds offset when accessing it
2016-01-23 Added code to read temperatures, lots more variables along with a way to set them and print out valid key value input. Also added basic control logic along with a way to start and stop it from the se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
2016-02-17 Added code to actually read sensors and run motors along with variables to suppor that code and some manual testing methods.
2016-03-10 Adding code to config inside and outside heat sensors separately. Also added config parameter to auto run the program on restart instead of waiting for serial input.
2016-03-13 Added RTC and heatwave sensing code, still need to enable heatwave holding
2016-03-13 Added code to enable artificial heatwaves and standardized spacing after //s
2016-03-14 Updated to check for heat wave log file and to test heat wave switch
2016-03-14 Added code to use PIR sensors to ensure no one is around while rolling sides for safety
2016-03-23 Added code to log limit switch hits better
2016-05-16 Semifinal version of the code with new pin defitions, no more battery checks. Only caveat is RTC code is still commented out because it may be crashing things
    [HighTunnelController.ino, PinDefinitions.txt.ino]
2016-05-20 Disabling SD card stuff, multisampling PIR and Temp sensors and moving some pins around
2016-05-20 Finalizing new pin definitions
2016-06-06 Sampling only 25 times to avoid int overflow
    [HighTunnelController.ino, PinDefinitions.txt.ino, PinTester.ino]
2017-06-30 Update and Rollover
    Adding in files from the gDrive.
    [BoM.xlsx, Fan Modeling.xlsx, Groups Signup.xlsx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]
